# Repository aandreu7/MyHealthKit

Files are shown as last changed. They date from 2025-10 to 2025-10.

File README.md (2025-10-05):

# MyHealthKit 🤖💊

MyHealthKit is a modular robotic system designed to store, manage, and dispense medicines autonomously.

## Table of Contents
- [Description](#description)
  - [Project Overview](#project-overview)
- [Tools & Dependencies](#tools--dependencies)
  - [Tools](#tools)
  - [Dependencies](#dependencies)
- [Setup & Install](#setup--install)
- [Software](#software)
- [Hardware](#hardware)
  - [Laser Cutting Machine](#laser-cutting-machine)
  - [3D Model](#3d-model)
  - [Components](#components)
  - [Circuit Design](#circuit-design)
- [App Functionalities](#app-functionalities)
- [Amazing Contributions](#amazing-contributions)
- [Demonstration](#demonstration)
- [To Do](#to-do)
- [References](#references)
- [Contributors](#contributors)
- [License](#license)

## Description
---

### Project Overview
MyHealthKit is a modular robotic system designed to store, manage, and dispense medicines autonomously. Built around a Raspberry Pi 4, the robot integrates sensors such as RPLidar for laser-based environment mapping and utilizes ROS Noetic for SLAM and navigation. The physical structure includes laser-cut wood and methacrylate parts, combined with custom-designed 3D-printed components to create a practical and compact storage mechanism.

The accompanying mobile application enhances usability, offering functions like medicine recognition through AI-based image analysis, symptom-based diagnosis suggestions, and medicine inventory management. Users interact seamlessly with the robot via intuitive QR-code-based navigation requests and visual medicine retrieval commands.

The software architecture relies on ROS packages for robust mapping, localization, and path-planning capabilities, enabling autonomous operation in dynamic indoor environments.

By integrating advanced sensor fusion, intuitive software interfaces, and precision-designed hardware, MyHealthKit provides a reliable medicine management solution tailored for home or clinical environments.

This project and its repository is divided into two big modules: MyHealthController, related to all code running within the physical robot (SLAM, Navigation, server...), and MyHealthCall, a React Native application used to interact with the robot.

<p align="center">
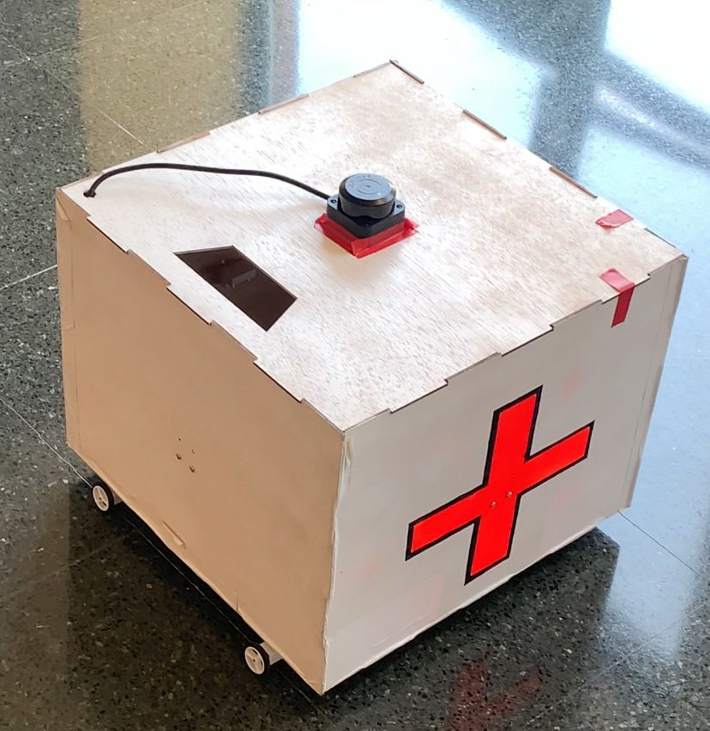
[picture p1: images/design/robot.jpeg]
  
</p>

## Tools & Dependencies
---
To fully develop the project, we rely on a set of specific tools and dependencies that help us achieve the expected results.

### Tools
* **[CoppeliaSim](https://www.coppeliarobotics.com/):** For robot simulation.  
* **[Visual Studio Code](https://code.visualstudio.com/):** For robot development with Python.  
* **[RViz](https://wiki.ros.org/rviz):** 3D visualization tool for ROS, useful for viewing robot models, sensor data, and planning information.  
* **[draw.io](https://app.diagrams.net/):** Diagramming tool for designing system architectures, flowcharts, and processes.  
* **[Fritzing](https://fritzing.org/):** Open-source tool for designing and documenting electronics and breadboard layouts.

### Dependencies
##### MyHealthController
- 
- 
- 
- 
- 
- 
- 
- 

##### MyHealthCall
- 
- 
- 

## Setup & Install
---
Download this repository.

git clone https://github.com/aandreu7/MyHealthKit

To run MyHealthCall app, follow these instructions:

- Install Node.js and Expo Go app.
- Go to MyHealthCall/
- Execute npm install in order to install all package.json dependencies.
- Execute npx expo start -c --tunnel
- App will be available on web trough http::/localhost
- To use it on phone, change local phone IP on MyHealthCall/services/sendMessageToRobot.tsx, press C and scan QR code using Expo Go app.

To run MyHealthController (server + hardware drivers), follow these instructions:

- To run server, go to MyHealthController/ and execute:

pip install -r requirements.txt

So as to install all Python dependencies.

- Execute MyHealthController/server/app.py using a Python3 interpreter and server will be running on port 5000 by default.

- Install ROS Noetic. Only available on Ubuntu 20.04 (Docker images are published but only working on Linux devices, not working on Windows/MacOS through Docker Desktop). Follow this tutorial to install and get familiarized with ROS: https://wiki.ros.org/noetic/Installation

- To run SLAM and Navigation, go to MyHealthController/SLAM/catkin_ws and compile it executing:

catkin_make

- Once compiled, run ROS (RPLidar C1 + Hector SLAM + move_base) using our personalized ROS packet and launch file:

roslaunch my_slam_setup myhealthkit.launch

## Software
---
This section explains the software architecture, describing how the robot's modules interact to perform coordinated tasks.

The following scheme illustrates how user can communicate with MyHealthKit through MyHealthCall application. A user can ask for a diagnosis, the list of medicines storaged in the robot, request the presence of the robot, and ask to add and store a new medicine.

The robot, as it runs a server on its controller, responds to each petition while runs SLAM continuously.
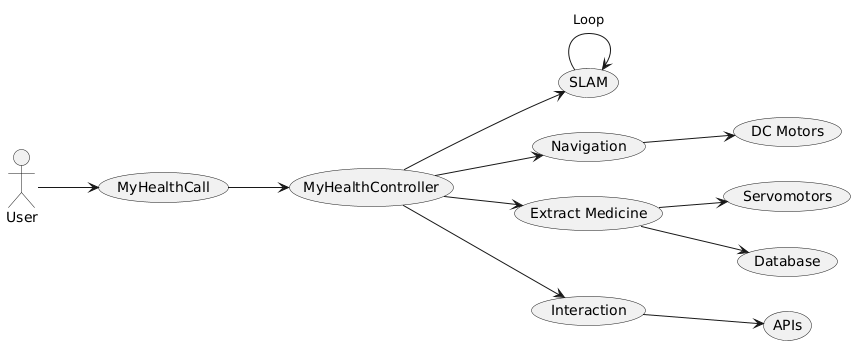
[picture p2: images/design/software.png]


Our project integrates ROS (Noetic), which works using topics and nodes. The following diagram shows how nodes publish data on topics, so other nodes can gather input data and produce and publish new data on output topics.

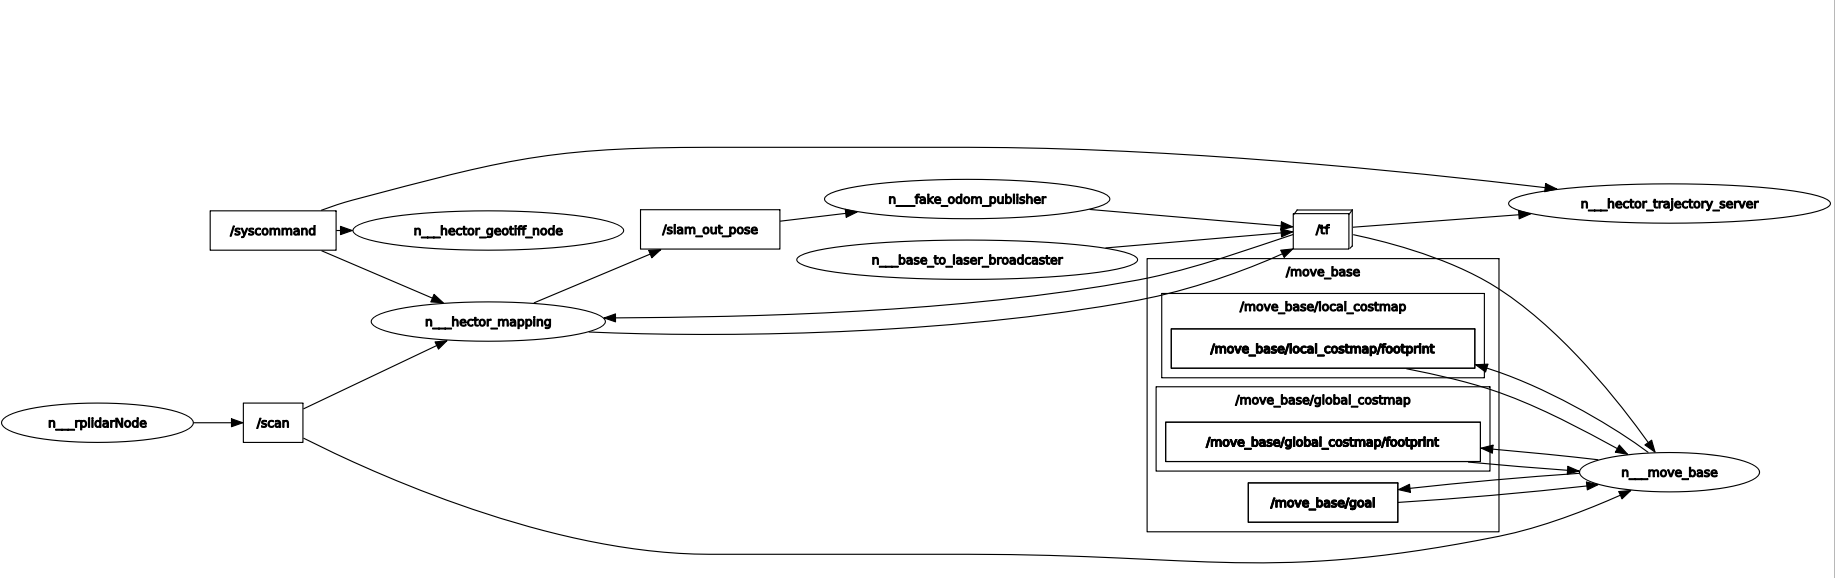
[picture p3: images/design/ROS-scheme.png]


Basically, RPLidar node publishes data on /scan topic, so Hector SLAM, through the implementation of a scan-matching algorithm, can create the map, which is sent to Move Base node, which publishes the velocity at which each wheel should run to get to the goal.

## Hardware
---
In this section, we describe the laser-cut parts, the 3D models used, the components table with prices, and the circuit design of MyHealthKit.

### Laser Cutting Machine
This section shows the laser-cut parts: methacrylate and wood for gears and structural elements.

| Methacrylate | Image | Wood | Image |
|---|---|---|---|
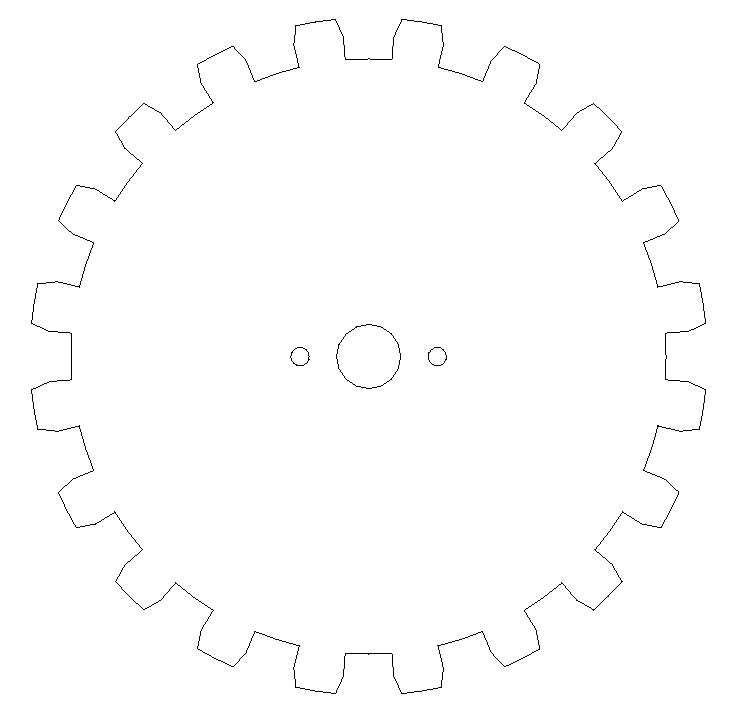
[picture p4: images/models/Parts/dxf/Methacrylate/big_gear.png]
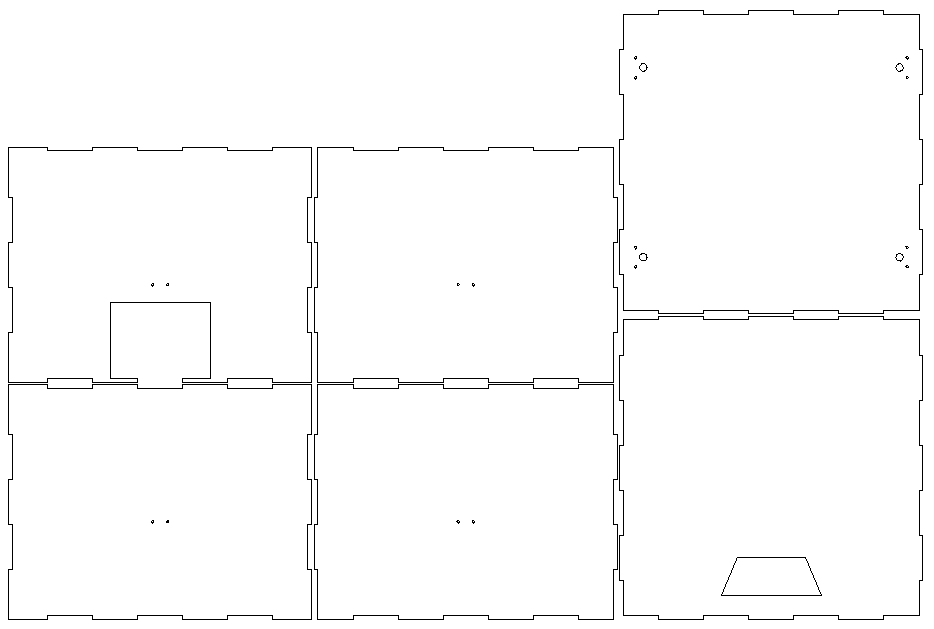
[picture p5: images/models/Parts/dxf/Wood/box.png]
| Big gear |  | Box |  |
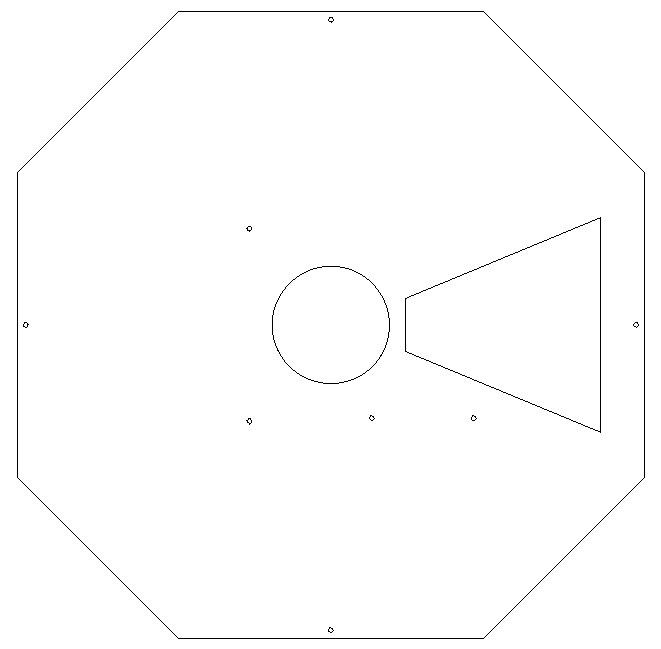
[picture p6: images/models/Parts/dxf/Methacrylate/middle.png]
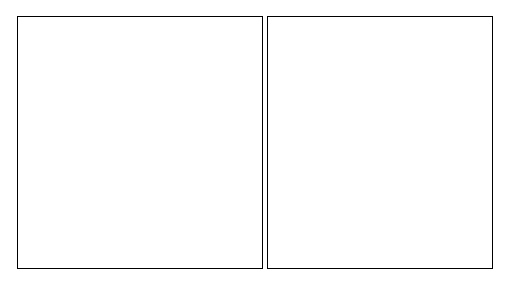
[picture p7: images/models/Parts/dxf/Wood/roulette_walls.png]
| Middle |  |  Roulette walls |  |
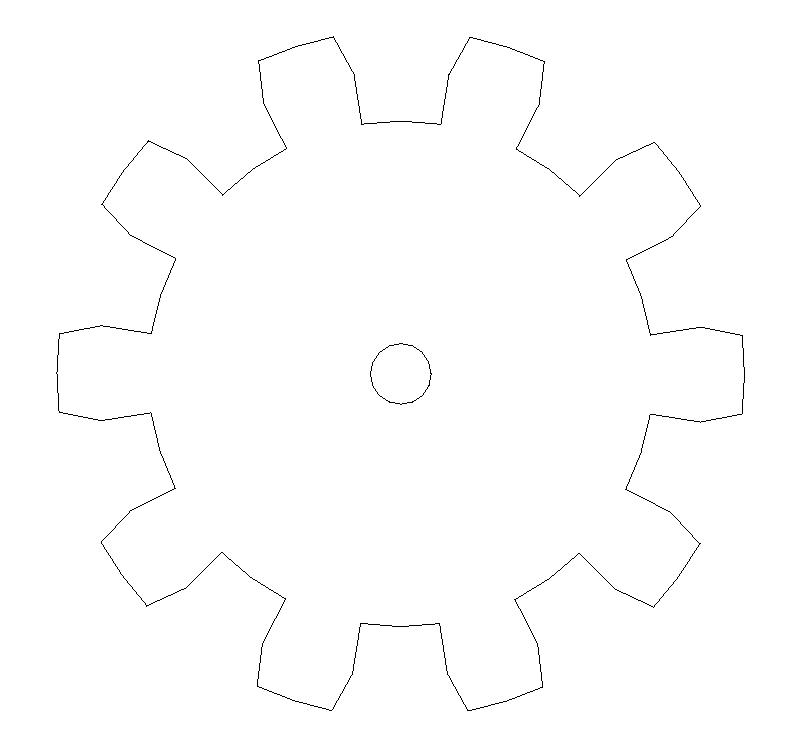
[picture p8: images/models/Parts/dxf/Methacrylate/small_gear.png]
| Small gear  |  |  | 

### 3D Model
Below we can see the complete structure of the MyHealthKit robot, both from the outside and the inside.

<table style="width:100%; table-layout:fixed;">
  <tr>
    <th style="width:20%;">3D Piece</th>
    <th style="width:30%;">Image</th>
    <th style="width:20%;">3D Piece</th>
    <th style="width:30%;">Image</th>
  </tr>
  <tr>
    <td>Outside</td>
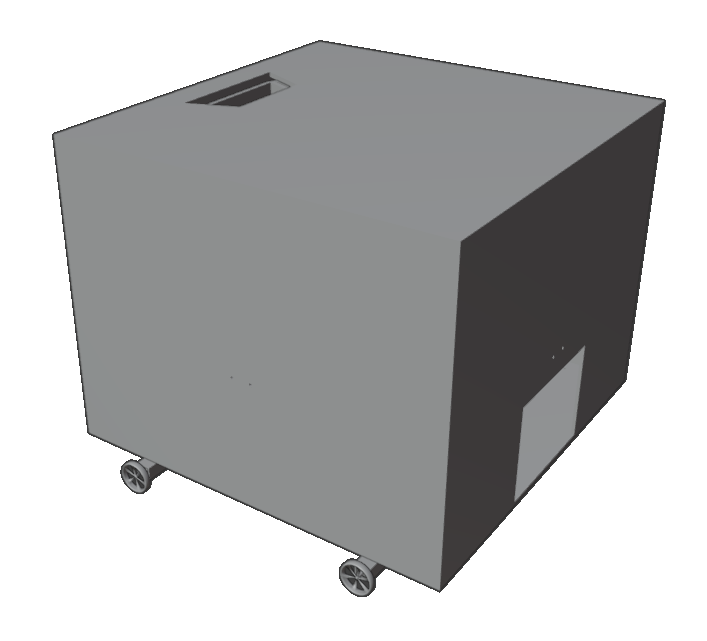
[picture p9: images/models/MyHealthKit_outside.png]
    <td></td>
    <td>Inside</td>
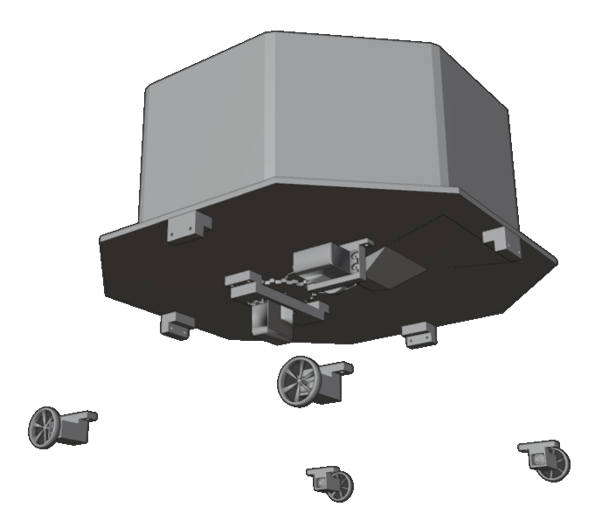
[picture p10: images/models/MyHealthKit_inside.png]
    <td></td>
  </tr>
</table>

The following section shows each 3D piece separately.
Each model corresponds to a physical part of the robot that was designed and printed individually for assembly.

| 3D Piece | Image | 3D Piece | Image |
|---|---|---|---|
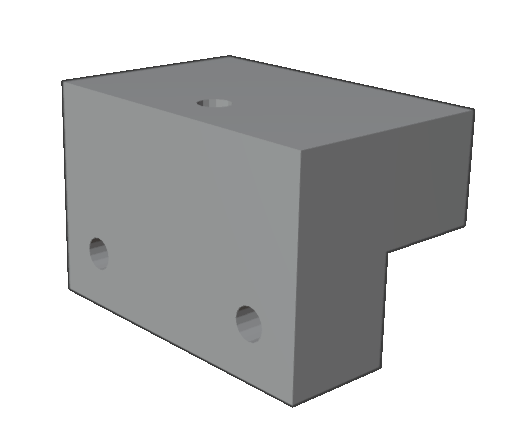
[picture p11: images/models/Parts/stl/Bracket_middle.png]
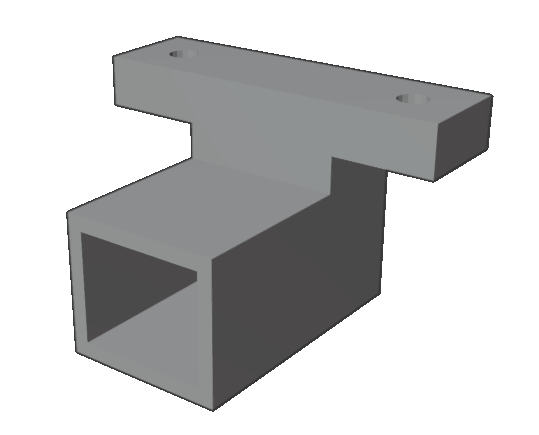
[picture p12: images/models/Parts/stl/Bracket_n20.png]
| Bracket middle |  | Bracket n20 |  |
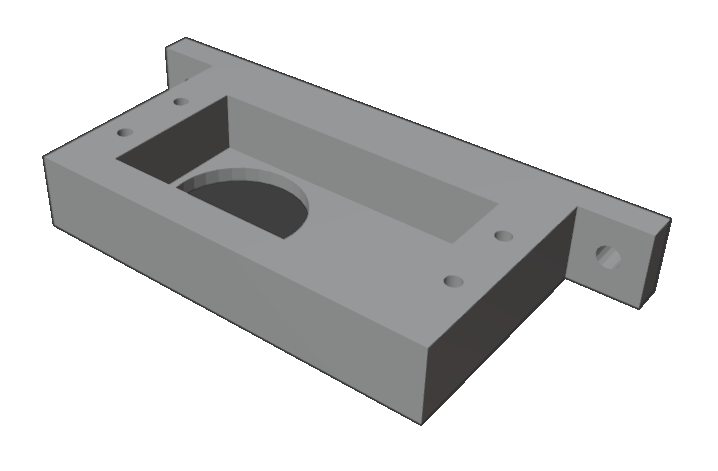
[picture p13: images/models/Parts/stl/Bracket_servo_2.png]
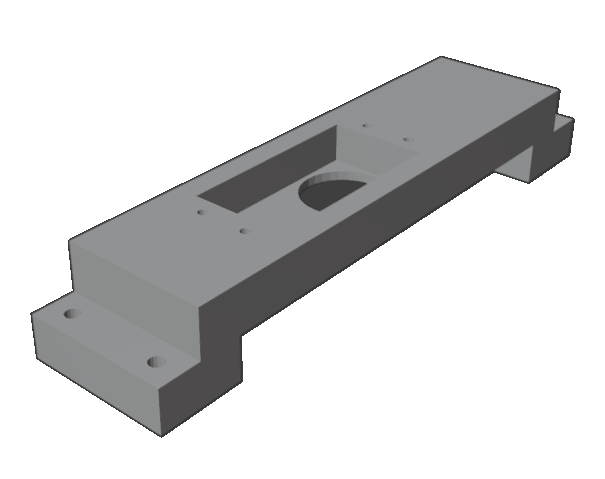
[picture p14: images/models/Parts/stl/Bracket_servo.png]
| Bracket servo trap door |  | Bracket servo roulette |  |
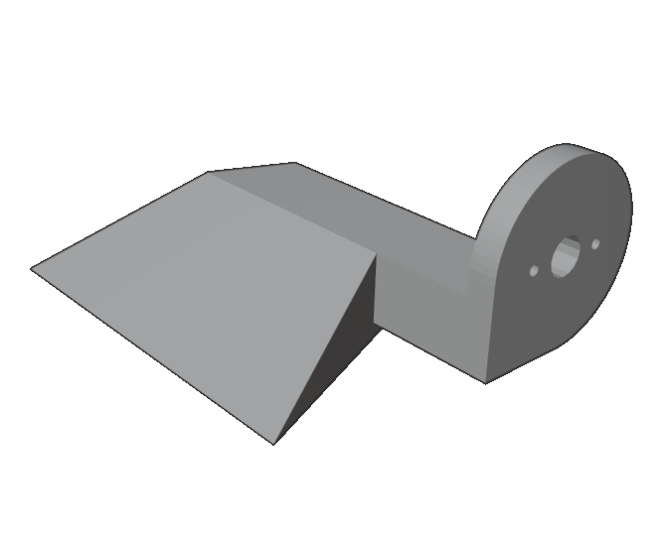
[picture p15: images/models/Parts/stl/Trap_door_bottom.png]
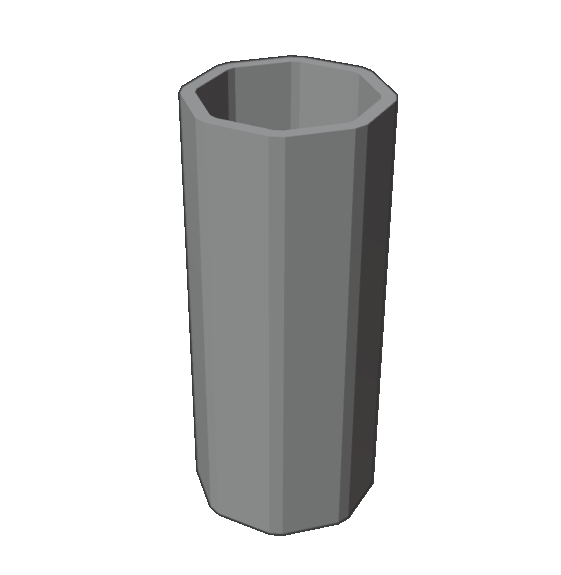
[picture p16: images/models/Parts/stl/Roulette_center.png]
| Trap door  |  | Roulette |  

### Components
In this section, we provide an overview of the key components 
| **Name** | **Units** | **Total** |
|---|---|---|
| Raspberry Pi 4 Modelo B 8GB RAM | 1 | 89.95€ |
| RPLidar C1 | 1 | 96.74€ |
| Controlador motor DC dual DRV8833 | 2 | 36.18€ |
| Batería Ion Litio 3.7V | 1 | 24.14€ |
| Servomotor MG996R | 2 | 15.74€ |
| Mini Motor DC | 4 | 12.12€ |
| Rueda de goma 32x7mm (2 und) | 2 | 9.56€ |
| **Total Price** | | **284.43€** |

### Circuit Design
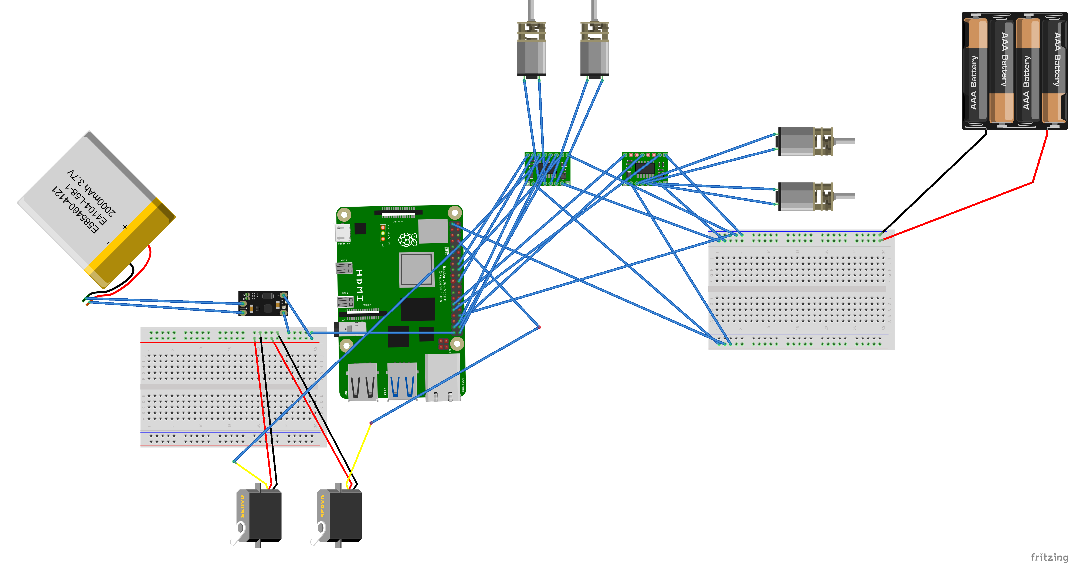
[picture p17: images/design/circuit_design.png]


## App Functionalities
---
This section covers the main app features, including direct interaction with the robot.  
**Figure 1** shows the app’s home screen, where all functions can be accessed.

### Add a medicine
This feature lets the user add a new medicine by taking a photo. An AI analyzes the image, saves the data, and the robot assigns a free slot for manual placement.  
**Figure 2** shows the capture interface.

### Get a Diagnosis
The user records their symptoms, and an AI analyzes the audio to suggest a diagnosis and matching medicines. The result is also spoken aloud through the phone.  
**Figure 3** shows an example of a diagnosis result.

### Show Medicines
This option allows the user to see the list of medicines stored in the robot.  
**Figure 4** shows an example with several items.
When selecting a medicine, options appear to retrieve or delete it, as shown in **Figure 5**. The app also provides information about the medicine.
Tapping *Get Medicine* makes the robot locate and release the item, which must later be returned to the same slot.  
Tapping *Delete Medicine* makes the item accessible for manual removal and deletes it from the system.

### Request MyHealthKit
Another functionality available on the Home screen is *Request MyHealthKit*, which lets the user scan a QR code representing a destination. The robot then moves automatically to that location.  
**Figure 6** shows the QR scanning process.

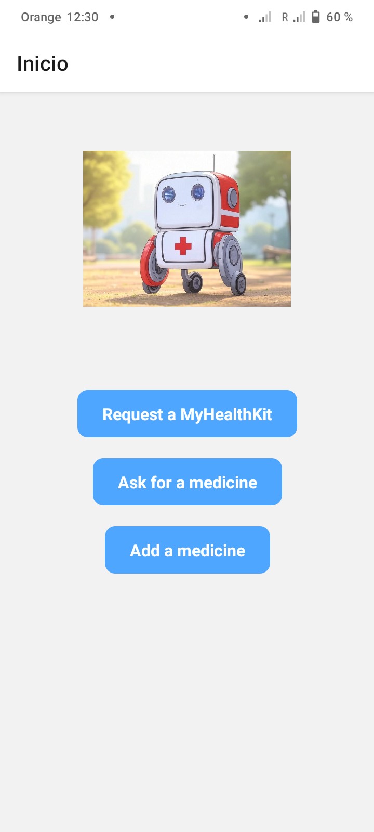
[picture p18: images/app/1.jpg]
Figura 1
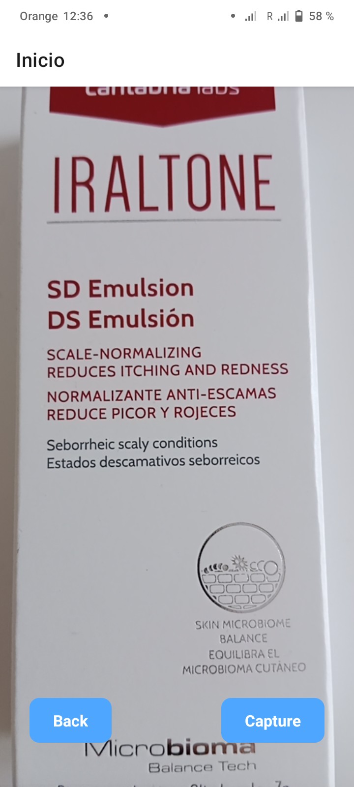
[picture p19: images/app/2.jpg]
Figura 2
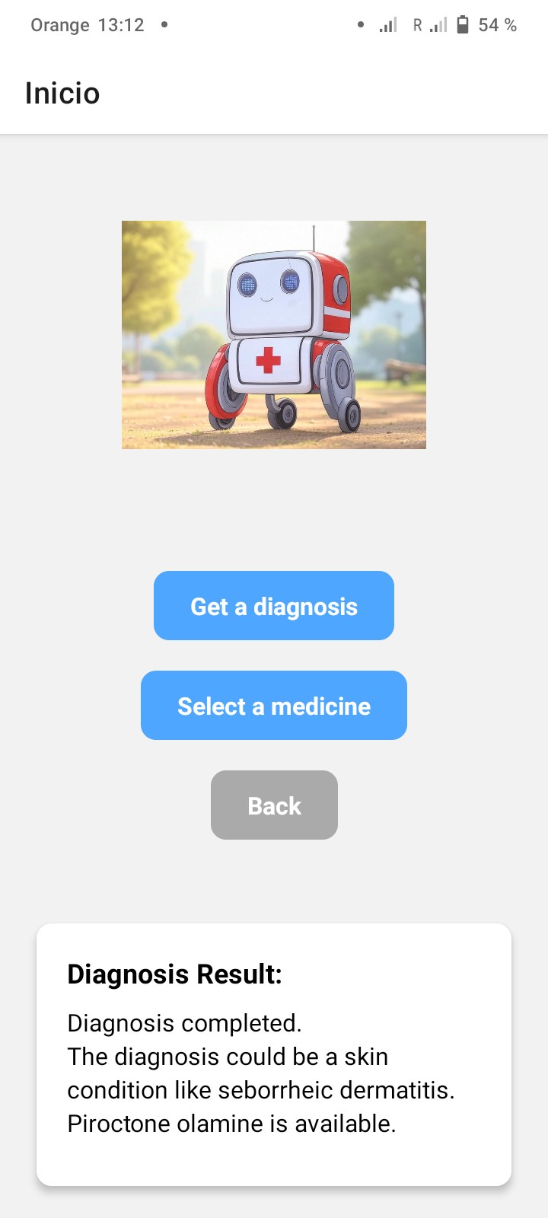
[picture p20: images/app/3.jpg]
Figura 3
|  |  |  |
|:---:|:---:|:---:|
| **Figura 1. Main screen** | **Figura 2. Medicine capture**  | **Figura 3. Diagnosis result**  |
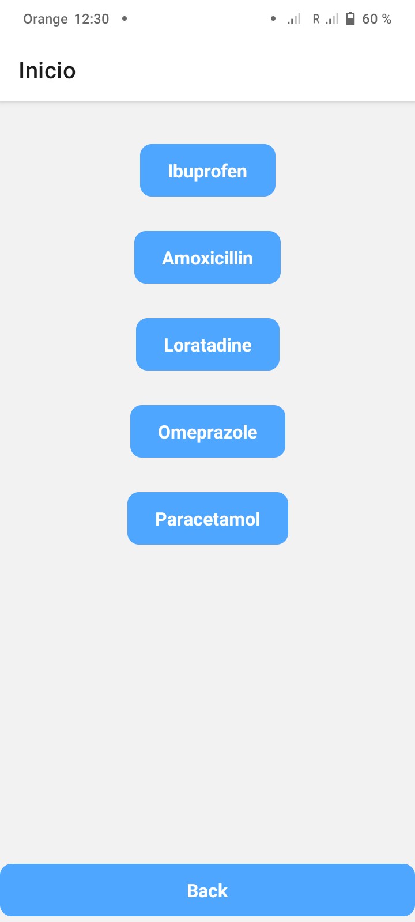
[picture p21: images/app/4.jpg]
Figura 4
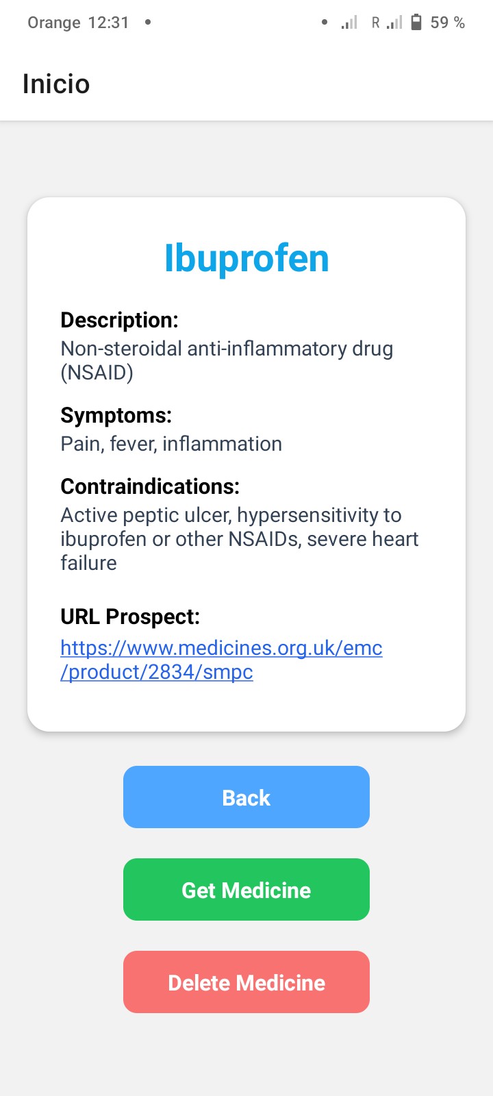
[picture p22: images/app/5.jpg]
Figura 5
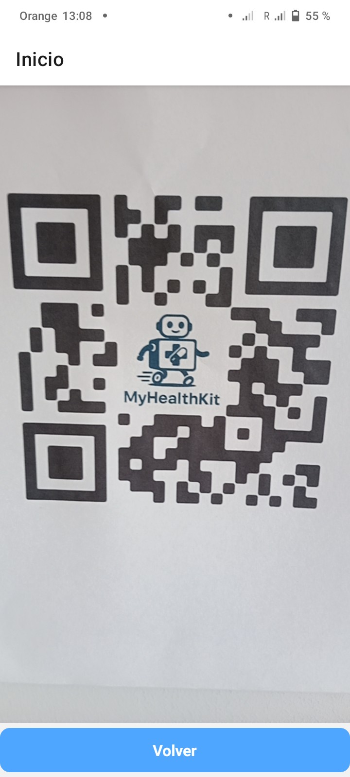
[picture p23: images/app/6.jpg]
Figura 6
|  |  | |
| **Figura 4. Stored medicines**  | **Figura 5. Details medicine**  | **Figura 6. Scanning QR** |

## Amazing Contributions
---
- One-click navigation: At any moment, just by scanning a QR code, which can be done with only one click on the app main screen, a MyHealthKit will automatically set sail to your position.

- Fully-integrated medical support: A MyHealthKit cannot only be used to store and deploy medicines, but also serves as a server able and prepared to respond to medical-related questions, give medical advices and diagnosis using a fine-tunned LLM model through MyHealthCall app.

## Demonstration
---
[Link to visual demonstration](https://youtu.be/2AqkAf-FRpg)

## To Do
---
- **Improved App-Robot Communication** Use WebSocket or MQTT instead of HTTP to enable real-time communication, lower latency, and better handling of asynchronous events like alerts or confirmations.

- **Enhanced App Interactivity** Add features that let users track if they took their medicine, mark follow-up days, and receive reminders, improving treatment adherence and user engagement.

## References
---
- i. React. (n.d.). *React documentation*. Retrieved June 26, 2025, from https://react.dev/
- ii. Hector SLAM. *Code and documentation*. Retrieved June 26, 2025, from https://wiki.ros.org/hector_slam
- iii. OpenAI. (n.d.). *API reference and model documentation*. Retrieved June 26, 2025, from https://platform.openai.com/docs
- iv. Together AI. (n.d.). *Together AI - Cloud inference and open models*. Retrieved June 26, 2025, from https://www.together.ai/

## Contributors
---
- **Zakaria Boudich Makran** - Universitat Autònoma de Barcelona (UAB)
- **Damià Turu Pérez** - Universitat Autònoma de Barcelona (UAB)
- **Andreu Plana Joya** - Universitat Autònoma de Barcelona (UAB)
- **Oussama Berrouhou Barrouhou** - Universitat Autònoma de Barcelona (UAB)
- **Èric Rodríguez de Sande** - Universitat Autònoma de Barcelona (UAB)

## License
---
This project is licensed under the [Apache-2.0 License](https://github.com/aandreu7/MyHealthKit/blob/main/LICENSE).

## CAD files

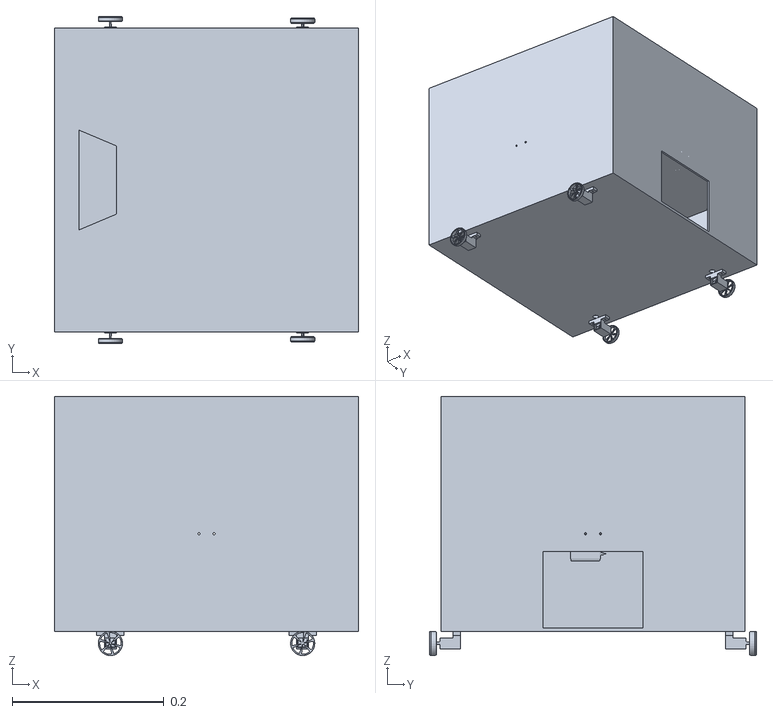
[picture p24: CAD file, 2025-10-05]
3D Models/MyHealthKit.stl
0.4 x 0.431 x 0.341

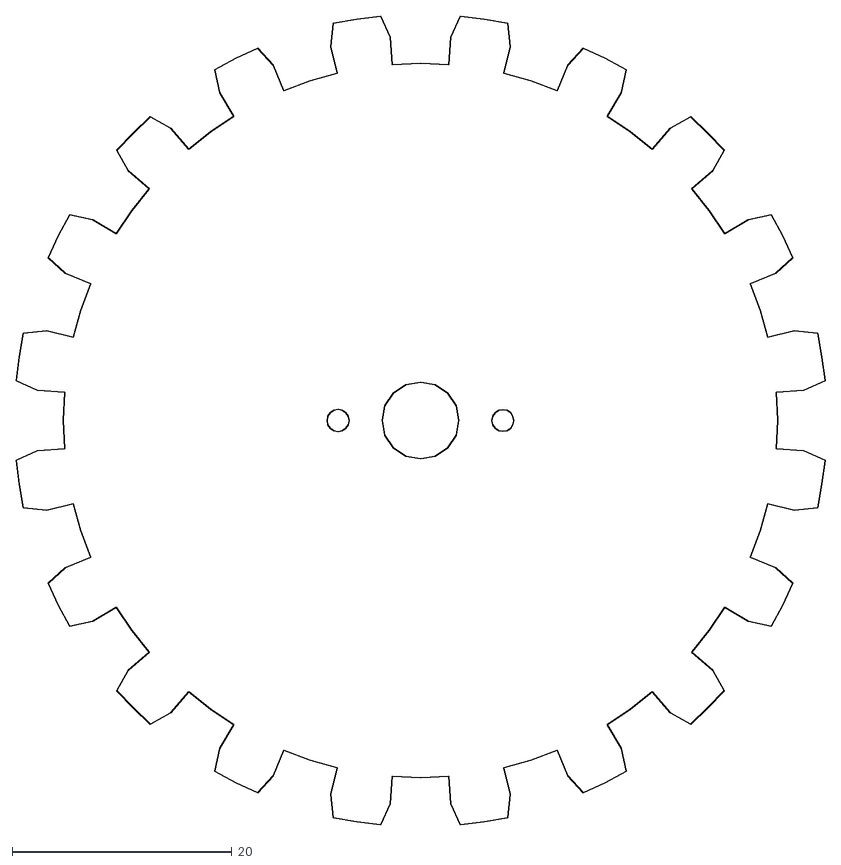
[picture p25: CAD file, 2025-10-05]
3D Models/Parts/dxf/Methacrylate/big_gear.dxf
73.6 x 73.6

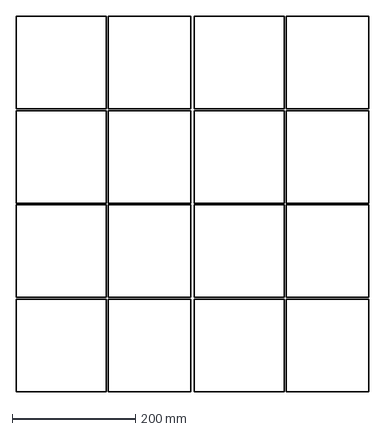
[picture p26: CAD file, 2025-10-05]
3D Models/Parts/dxf/Wood/roulette_walls_all.dxf
571.9 x 609.0 mm

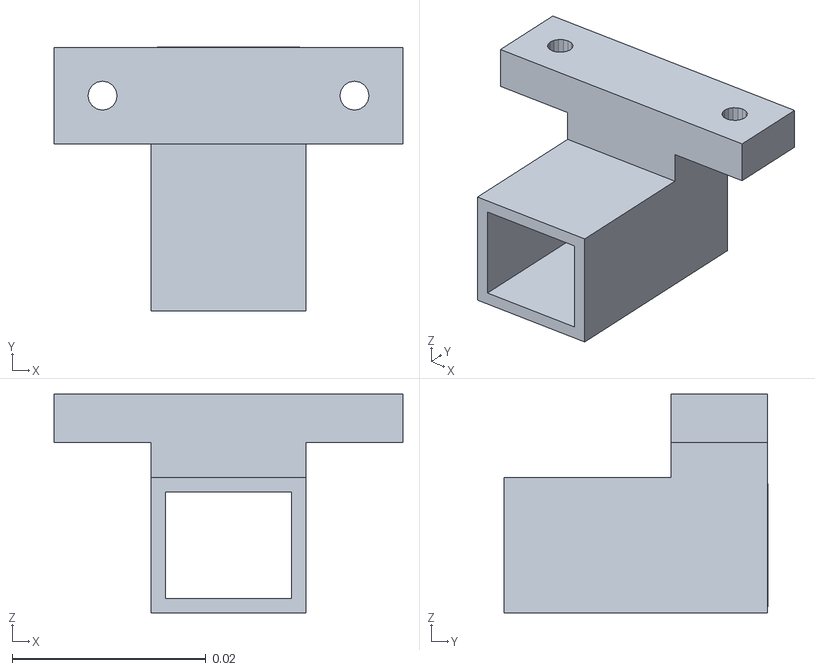
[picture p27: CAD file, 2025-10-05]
3D Models/Parts/stl/Bracket_n20.stl
0.0361 x 0.0272 x 0.0226

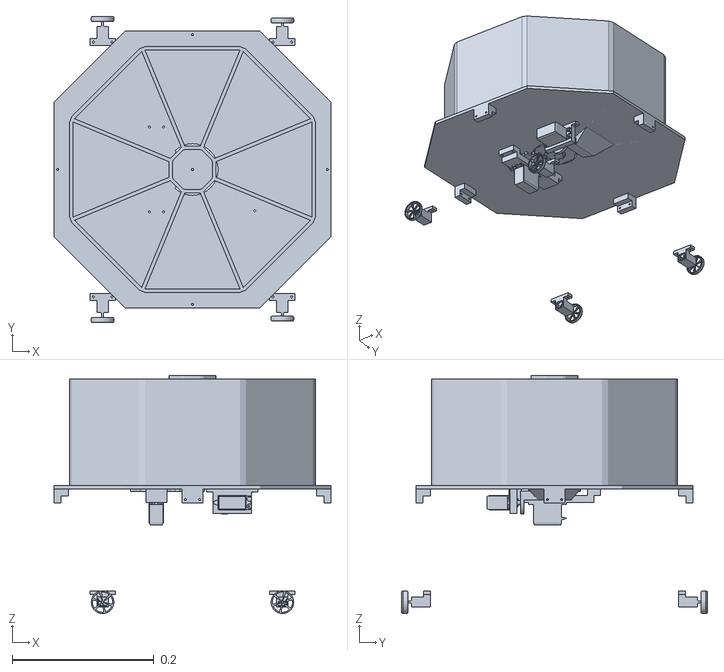
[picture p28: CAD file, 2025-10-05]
3D Models/MyHealthKit_inside.stl
0.39 x 0.431 x 0.335

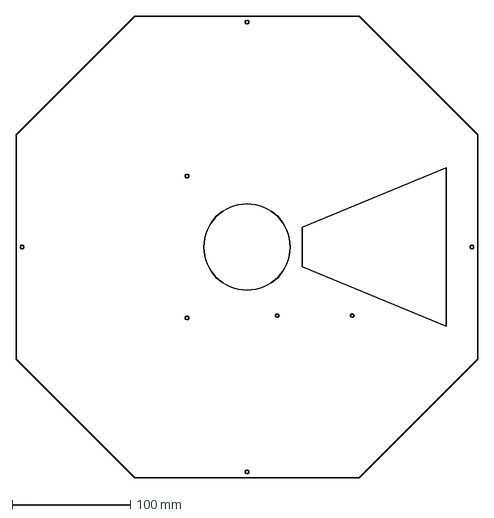
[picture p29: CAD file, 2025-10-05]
3D Models/Parts/dxf/Methacrylate/middle.dxf
390.0 x 390.0 mm

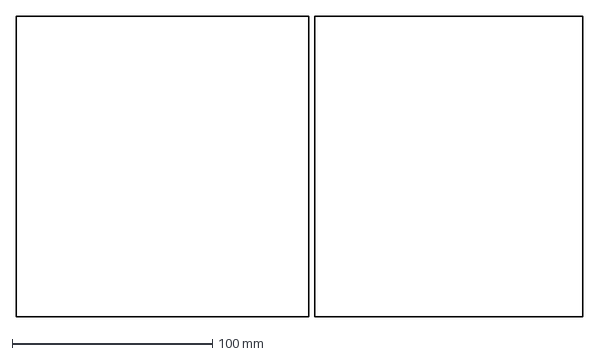
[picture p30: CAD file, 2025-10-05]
3D Models/Parts/dxf/Wood/roulette_walls.dxf
282.9 x 150.0 mm

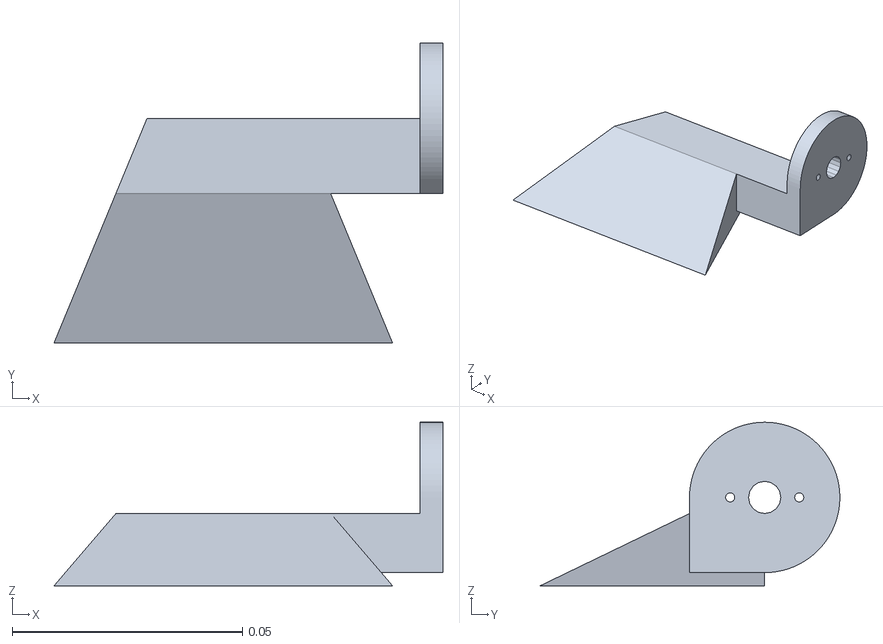
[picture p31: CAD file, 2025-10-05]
3D Models/Parts/stl/Trap_door_bottom.stl
0.0845 x 0.0651 x 0.0355

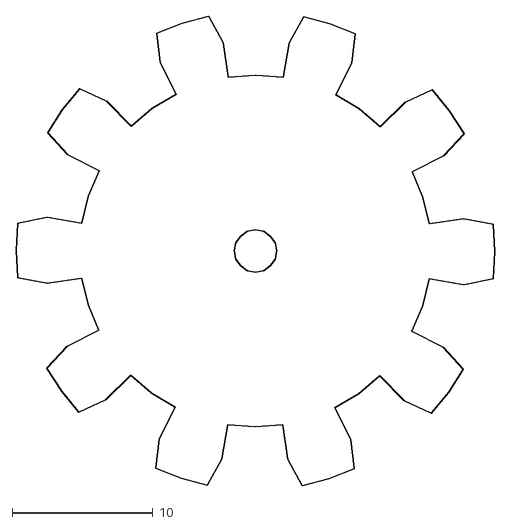
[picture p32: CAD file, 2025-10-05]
3D Models/Parts/dxf/Methacrylate/small_gear.dxf
34.0 x 33.3

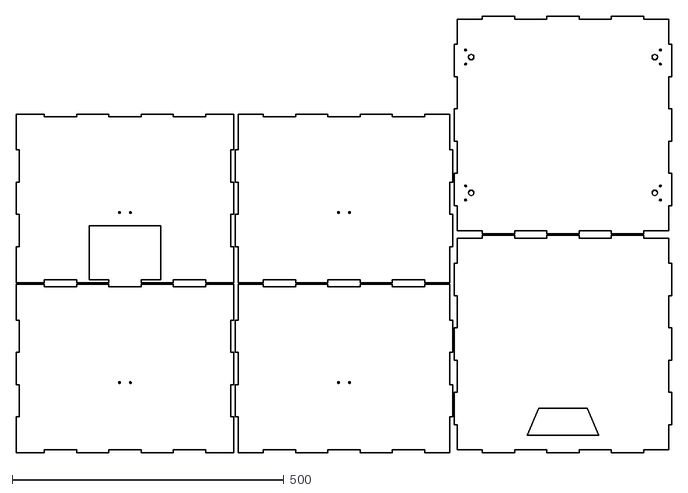
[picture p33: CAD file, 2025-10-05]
3D Models/Parts/dxf/Wood/box.dxf
1206.0 x 803.0

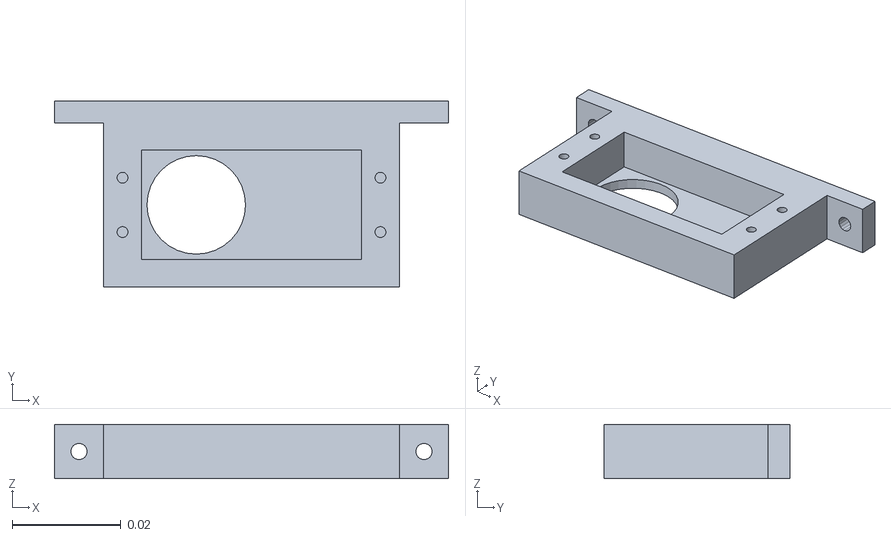
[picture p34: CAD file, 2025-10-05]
3D Models/Parts/stl/Bracket_servo_2.stl
0.0724 x 0.0341 x 0.01

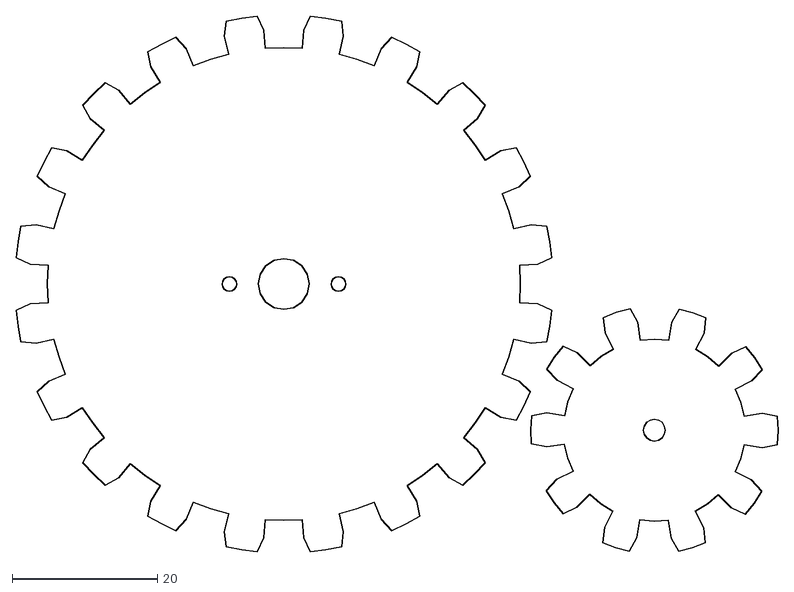
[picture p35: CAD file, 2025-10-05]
3D Models/Parts/dxf/Methacrylate/gears.dxf
104.7 x 73.6

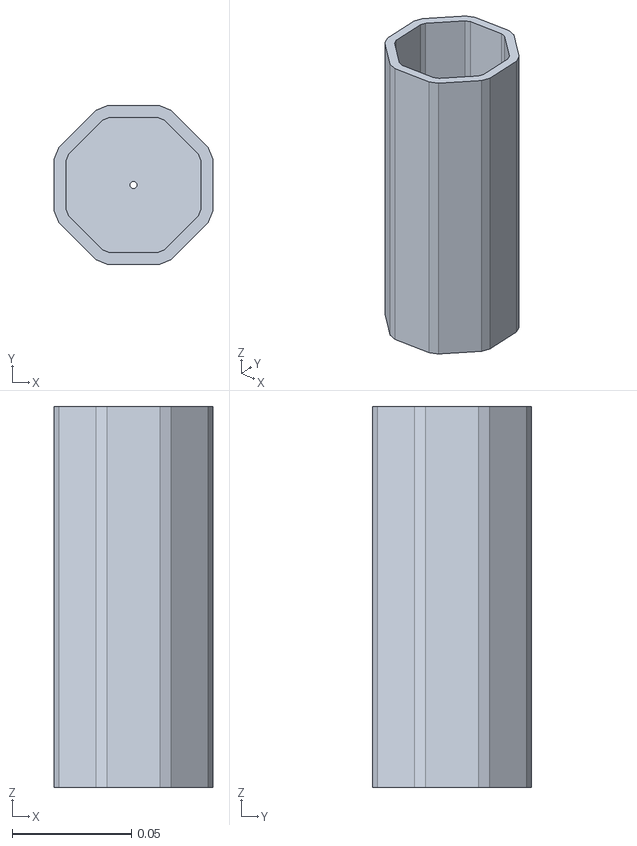
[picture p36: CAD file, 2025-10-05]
3D Models/Parts/stl/Roulette_center.stl
0.0666 x 0.0666 x 0.16

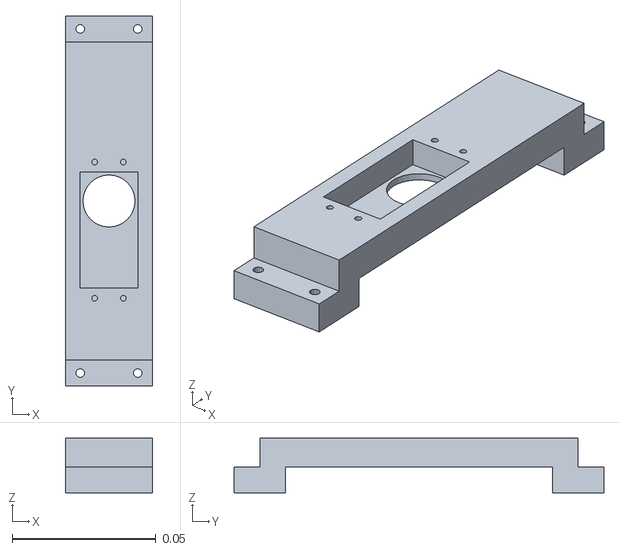
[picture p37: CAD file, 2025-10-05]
3D Models/Parts/stl/Bracket_servo.stl
0.0301 x 0.129 x 0.019

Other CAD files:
3D Models/Parts/stl/Bracket_middle.stl

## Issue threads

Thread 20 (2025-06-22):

Logic error Adding a Medicine

aandreu7, 2025-06-22:
When a photo of a medicine is taken, and it is sent to server, we are not currently checking if that medicine already exists on the database, nor if the storage is full.

Closed 2025-06-29.

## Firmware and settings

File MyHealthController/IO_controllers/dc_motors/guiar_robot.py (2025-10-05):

#!/usr/bin/env python3
import RPi.GPIO as GPIO
import time
import getch

# Pines BCM
STBY1 = 17
STBY2 = 26
PWM_FR = 24
PWM_FL = 23
PWM_BL = 5
PWM_BR = 6
AIN1_B = 25
AIN2_B = 16
BIN1_B = 21
BIN2_B = 20

FREQ = 500

def setup_motors():
    GPIO.setmode(GPIO.BCM)
    GPIO.setup([STBY1, STBY2, PWM_FR, PWM_FL, PWM_BR, PWM_BL,
                AIN1_B, AIN2_B, BIN1_B, BIN2_B], GPIO.OUT)

    pwm_FR = GPIO.PWM(PWM_FR, FREQ)
    pwm_FL = GPIO.PWM(PWM_FL, FREQ)
    pwm_BR = GPIO.PWM(PWM_BR, FREQ)
    pwm_BL = GPIO.PWM(PWM_BL, FREQ)

    pwm_FR.start(0)
    pwm_FL.start(0)
    pwm_BR.start(0)
    pwm_BL.start(0)

    GPIO.output(STBY1, GPIO.HIGH)
    GPIO.output(STBY2, GPIO.HIGH)

    # Dirección por defecto: adelante
    GPIO.output(AIN1_B, GPIO.LOW)
    GPIO.output(AIN2_B, GPIO.HIGH)
    GPIO.output(BIN1_B, GPIO.HIGH)
    GPIO.output(BIN2_B, GPIO.LOW)

    return pwm_FR, pwm_FL, pwm_BR, pwm_BL

def stop_motors(pwms):
    for pwm in pwms:
        pwm.ChangeDutyCycle(0)

def set_forward_direction():
    GPIO.output(AIN1_B, GPIO.LOW)
    GPIO.output(AIN2_B, GPIO.HIGH)
    GPIO.output(BIN1_B, GPIO.HIGH)
    GPIO.output(BIN2_B, GPIO.LOW)

def set_reverse_turn_direction():
    GPIO.output(AIN1_B, GPIO.HIGH)
    GPIO.output(AIN2_B, GPIO.LOW)
    GPIO.output(BIN1_B, GPIO.LOW)
    GPIO.output(BIN2_B, GPIO.HIGH)

def main():
    pwm_FR, pwm_FL, pwm_BR, pwm_BL = setup_motors()
    pwms = [pwm_FR, pwm_FL, pwm_BR, pwm_BL]

    print("Control WASD:")
    print("W = Adelante | A/D = Gira avanzando | S = Lento | X = Gira marcha atrás")
    print("ESPACIO = FRENAR | Q = Salir")

    try:
        while True:
            key = getch.getch().lower()

            if key == 'w':
                print("Adelante recto")
                set_forward_direction()
                pwm_FR.ChangeDutyCycle(100)
                pwm_FL.ChangeDutyCycle(100)
                pwm_BR.ChangeDutyCycle(100)
                pwm_BL.ChangeDutyCycle(100)

            elif key == 'a':
                print("Gira izquierda")
                set_forward_direction()
                pwm_FR.ChangeDutyCycle(100)
                pwm_FL.ChangeDutyCycle(30)
                pwm_BR.ChangeDutyCycle(100)
                pwm_BL.ChangeDutyCycle(30)

            elif key == 'd':
                print("Gira derecha")
                set_forward_direction()
                pwm_FR.ChangeDutyCycle(30)
                pwm_FL.ChangeDutyCycle(100)
                pwm_BR.ChangeDutyCycle(30)
                pwm_BL.ChangeDutyCycle(100)

            elif key == 's':
                print("Más lento recto")
                set_forward_direction()
                pwm_FR.ChangeDutyCycle(50)
                pwm_FL.ChangeDutyCycle(50)
                pwm_BR.ChangeDutyCycle(50)
                pwm_BL.ChangeDutyCycle(50)

            elif key == 'x':
                print("🔁 Gira marcha atrás (mantener pulsado)")
                set_reverse_turn_direction()
                pwm_FR.ChangeDutyCycle(100)
                pwm_FL.ChangeDutyCycle(100)
                pwm_BR.ChangeDutyCycle(100)
                pwm_BL.ChangeDutyCycle(100)

            elif key == ' ':
                print("🚨 FRENADO")
                stop_motors(pwms)

            elif key == 'q':
                print("Saliendo...")
                stop_motors(pwms)
                break

            else:
                print("Tecla no válida. Usa W/A/S/D/X/ESPACIO/Q")
                stop_motors(pwms)

    finally:
        stop_motors(pwms)
        for pwm in pwms:
            pwm.stop()
        GPIO.output(STBY1, GPIO.LOW)
        GPIO.output(STBY2, GPIO.LOW)
        GPIO.cleanup()
        print("GPIO limpiados. Programa finalizado.")

if __name__ == "__main__":
    main()

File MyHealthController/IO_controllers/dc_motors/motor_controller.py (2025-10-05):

import rospy
from geometry_msgs.msg import Twist
from gpiozero import PWMOutputDevice, DigitalOutputDevice

# --------------------------
# GPIO pins configuration
# Each motor uses 2 pins for direction and PWM control
#
# Left side motors
LEFT_FRONT_IN1 = 18
LEFT_FRONT_IN2 = 27
LEFT_REAR_IN1 = 24
LEFT_REAR_IN2 = 25

# Right side motors
RIGHT_FRONT_IN1 = 22
RIGHT_FRONT_IN2 = 23
RIGHT_REAR_IN1 = 5
RIGHT_REAR_IN2 = 6

# Standby pin (required by TB6612FNG motor driver)
STBY_PIN = 21  # Adjust this GPIO pin as needed

# --------------------------
# Initialize PWMOutputDevice for each motor pin
# This allows software PWM for speed control in both directions

# Left motors
left_front_in1 = PWMOutputDevice(LEFT_FRONT_IN1)
left_front_in2 = PWMOutputDevice(LEFT_FRONT_IN2)
left_rear_in1 = PWMOutputDevice(LEFT_REAR_IN1)
left_rear_in2 = PWMOutputDevice(LEFT_REAR_IN2)

# Right motors
right_front_in1 = PWMOutputDevice(RIGHT_FRONT_IN1)
right_front_in2 = PWMOutputDevice(RIGHT_FRONT_IN2)
right_rear_in1 = PWMOutputDevice(RIGHT_REAR_IN1)
right_rear_in2 = PWMOutputDevice(RIGHT_REAR_IN2)

# Initialize STBY pin to enable motor driver
stby = DigitalOutputDevice(STBY_PIN)
stby.on()  # Set HIGH to enable the motor driver

# --------------------------
def set_motor_speed(in1_front, in2_front, in1_rear, in2_rear, speed):
    """
    Controls speed and direction of two motors on one side.
    :param in1_front: PWMOutputDevice for front motor IN1
    :param in2_front: PWMOutputDevice for front motor IN2
    :param in1_rear: PWMOutputDevice for rear motor IN1
    :param in2_rear: PWMOutputDevice for rear motor IN2
    :param speed: float [-1.0 .. 1.0], positive = forward, negative = backward
    """
    if speed > 0:
        # Forward motion: PWM on IN1, 0 on IN2
        in1_front.value = speed
        in2_front.value = 0
        in1_rear.value = speed
        in2_rear.value = 0
    elif speed < 0:
        # Reverse motion: PWM on IN2, 0 on IN1
        in1_front.value = 0
        in2_front.value = -speed
        in1_rear.value = 0
        in2_rear.value = -speed
    else:
        # Stop motors
        in1_front.value = 0
        in2_front.value = 0
        in1_rear.value = 0
        in2_rear.value = 0

# --------------------------
def cmd_vel_callback(msg):
    """
    Callback for /cmd_vel topic.
    Converts linear and angular velocities to left and right motor speeds.
    """
    linear = msg.linear.x      # Forward/backward speed (m/s)
    angular = msg.angular.z    # Rotation speed (rad/s)

    # Distance between wheels (meters), adjust to your robot
    wheel_base = 0.20

    # Compute speed for left and right side (differential drive)
    speed_right = linear + (angular * wheel_base / 2.0)
    speed_left = linear - (angular * wheel_base / 2.0)

    # Normalize speeds so neither exceeds abs(1.0)
    max_speed = max(abs(speed_left), abs(speed_right), 1.0)
    speed_left /= max_speed
    speed_right /= max_speed

    # Apply speeds to motors
    set_motor_speed(left_front_in1, left_front_in2, left_rear_in1, left_rear_in2, speed_left)
    set_motor_speed(right_front_in1, right_front_in2, right_rear_in1, right_rear_in2, speed_right)

# --------------------------
def main():
    rospy.init_node('motor_controller')
    rospy.Subscriber('/cmd_vel', Twist, cmd_vel_callback)
    rospy.loginfo("Motor controller node started, waiting for /cmd_vel messages...")
    rospy.spin()

if __name__ == '__main__':
    main()

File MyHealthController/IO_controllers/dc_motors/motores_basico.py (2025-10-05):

import RPi.GPIO as GPIO
import time

# Pines que estamos usando
STBY = 17    # STBY del driver
PWMA = 23    # PWM del Motor A
PWMB = 24    # PWM del Motor B

# Configuración
GPIO.setmode(GPIO.BCM)
GPIO.setup(STBY, GPIO.OUT)
GPIO.setup(PWMA, GPIO.OUT)
GPIO.setup(PWMB, GPIO.OUT)

# Configuramos PWM a 500 Hz
pwm_a = GPIO.PWM(PWMA, 500)
pwm_b = GPIO.PWM(PWMB, 500)
pwm_a.start(50)  # 50% duty cycle
pwm_b.start(50)  # 50% duty cycle

# Activar el driver
GPIO.output(STBY, GPIO.HIGH)

try:
    print("Los motores deberían girar ahora...")
    time.sleep(10)  # Mantener girando 10 segundos
finally:
    pwm_a.stop()
    pwm_b.stop()
    GPIO.cleanup()
    print("Motores parados y GPIO limpiados")

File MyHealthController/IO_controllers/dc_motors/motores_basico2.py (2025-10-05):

#!/usr/bin/env python3
from gpiozero import PWMOutputDevice, DigitalOutputDevice
from time import sleep

# Pines BCM
STBY   = DigitalOutputDevice(17)  # STBY a GPIO17
motorA = PWMOutputDevice(23)      # PWMA a GPIO23
motorB = PWMOutputDevice(24)      # PWMB a GPIO24

try:
    # Habilita el driver
    STBY.on()
    sleep(0.1)

    print("Motores al 60% durante 5 s…")
    motorA.value = 0.6
    motorB.value = 0.6
    sleep(5)

    print("Motores al 30% durante 5 s…")
    motorA.value = 0.3
    motorB.value = 0.3
    sleep(5)

    print("Deteniendo motores…")
    motorA.value = 0
    motorB.value = 0
    sleep(1)

finally:
    motorA.close()
    motorB.close()
    STBY.close()
    print("GPIO limpiados, fin del script.")

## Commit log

2025-04-26 Mensaje de tu commit aquí
2025-05-30 Create start-slam.sh
    This file is automatically executed when Raspberry is connected to WiFi
2025-06-23 Bug fixing. Spin Wheel function
2025-06-24 Add folder with the 3D models
    In this folder there is the next content:
    - MyHealthKit.stl: The complete model.
    - Parts:
    - dxf: Pieces cut with the laser cutting machine, depending on the material it is splitted into two folders: Wood or Methacrilate.
    - stl: Pieces printed with the 3D printer.
    [Bracket_middle.stl, Bracket_n20.stl, Bracket_servo.stl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]
2025-06-25 Add model without the box
    This model excludes the box in order to make the inside components visible.
    [MyHealthKit_inside.stl]
2025-06-25 MyHealthKit_inside model correction
    [MyHealthKit_inside.stl]
